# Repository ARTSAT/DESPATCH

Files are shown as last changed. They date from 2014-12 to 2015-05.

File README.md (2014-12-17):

Hardware / Software design of ARTSAT2:DESPATCH
========
This repository is for hardware / software design of ARTSAT2:DESPATCH.  

o spacecraft/body : contains DESPATCH's body design and CAD data.  
o spacecraft/main : contains main OBC's CAD data and source codes.  
o spacecraft/mission : contains mission OBC's CAD data and source codes.  
o ground_station/decoder :  contains telemetry decoding software.  
o ground_station/tracker :  contains tracking software.  
o ground_station/server : contains API server software.  
o ground_station/utility : contains some utility software such as a viewer or an editor, etc...  
o document : contains some specifications of morse and baudot code format, etc...

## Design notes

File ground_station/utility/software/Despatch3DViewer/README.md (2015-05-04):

Despatch3DViewer
====
A 3D viewer for DESPATCH, writted in Javascript.

## Description

[DESPATCH](http://artsat.jp/en/project/despatch), a micro space-probe developed by ARTSAT project, can be viewed on your browser. 
You can zoom in/out and rotate the spacecraft.

## Demo

http://mokk.net/despatch3d/

## Screen shot

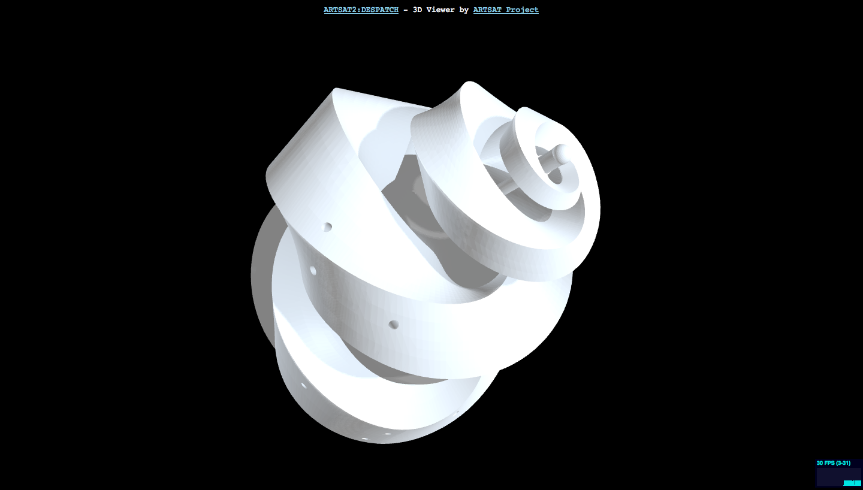
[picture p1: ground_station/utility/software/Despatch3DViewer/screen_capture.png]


## Requirement

A browser that supports WebGL (Google Chrome is recommended).

## Licence

This software is released under the MIT License, see LICENSE.txt.

## Author

[Motoki Kimura](https://github.com/motokimura)

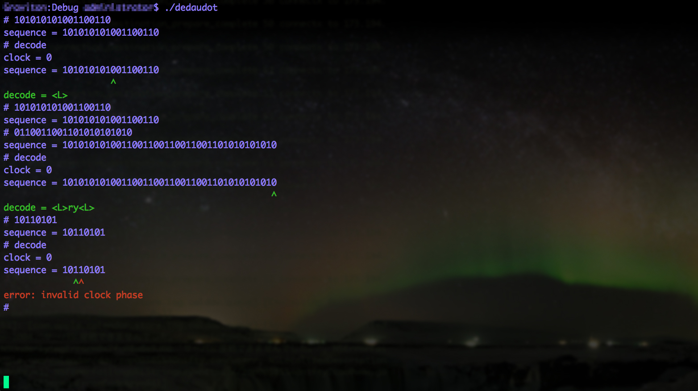
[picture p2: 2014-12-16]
ground_station/decoder/software/debaudot/debaudot_screen2.jpg

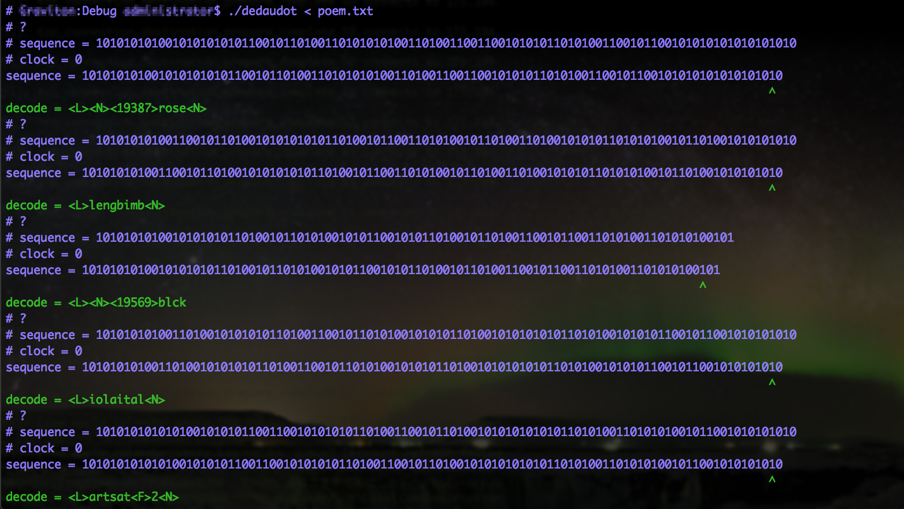
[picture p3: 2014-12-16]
ground_station/decoder/software/debaudot/debaudot_screen1.jpg

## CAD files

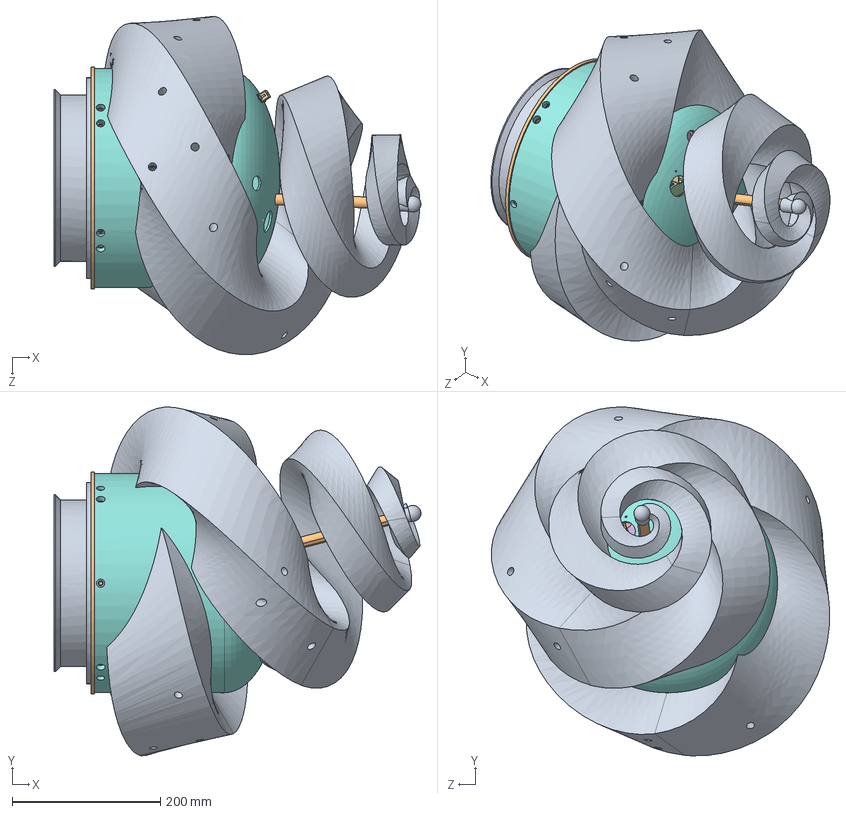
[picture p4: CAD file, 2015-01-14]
spacecraft/body/hardware/SOLIDWORKS/FM_ver1_4/DESPATCH_Assembly.SLDASM
495.6 x 470.8 x 456.7 mm
PAF_interface_frame
Base_Plate2
battery_case_bottom
Aluminium_Keel
Battery x 14
Battery_Case_Top
M3×25_spacer x 4
Aluminium_Cover
Sculpture
Support_rod
Dsub_9pin_female
OBC
M3×5_spacer x 4
Transmitter
Electromagnetic_Shield
Supporting_pole x 6
M2.6×2_spacer x 2
Battery_hub_board
M3×12CAP x 4
hub_insulator
M2.6×15CAP x 2
M2.5_nut x 2
Dsub_9pin_male

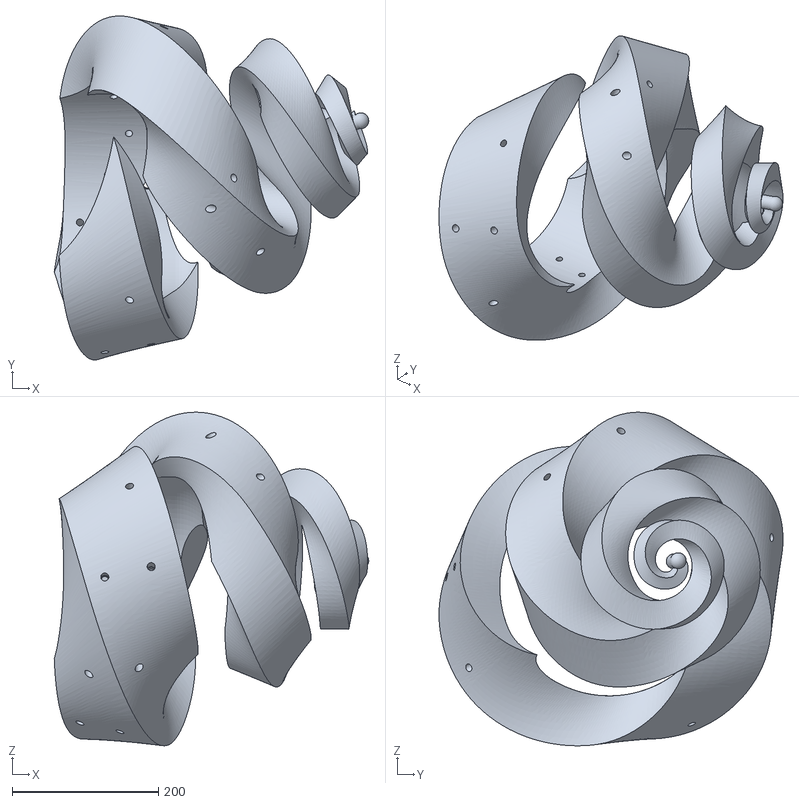
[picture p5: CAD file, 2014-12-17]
ground_station/utility/software/Despatch3DViewer/models/despatch_uzumaki.stl
430.8 x 471.2 x 457.0

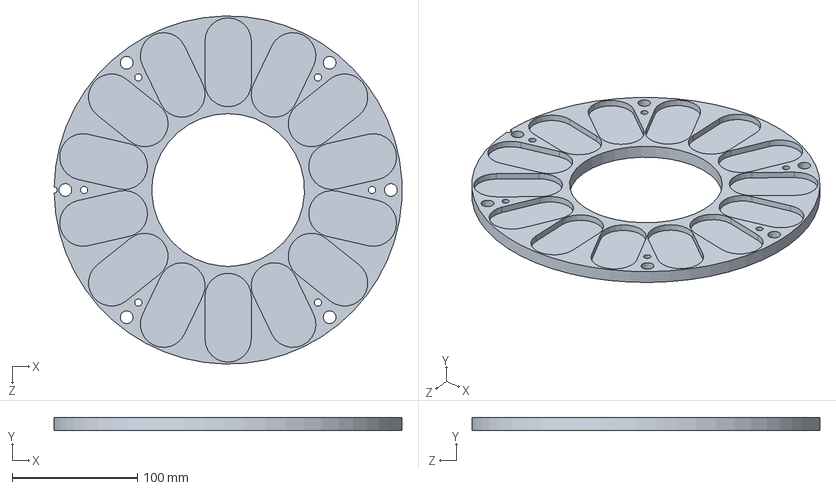
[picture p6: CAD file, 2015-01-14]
spacecraft/body/hardware/SOLIDWORKS/FM_ver1_4/Battery_Case_Bottom.SLDPRT
277.7 x 10.0 x 277.9 mm

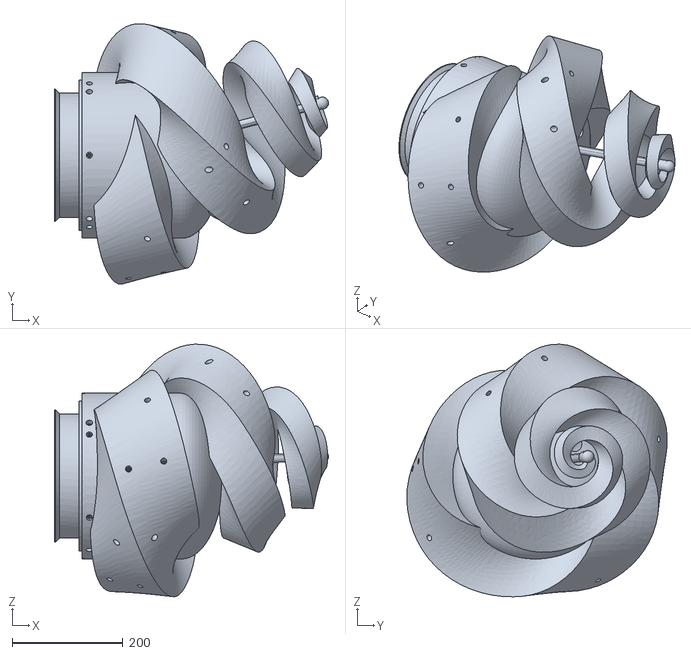
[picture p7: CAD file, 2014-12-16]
spacecraft/body/hardware/STL/FM_ver1.3.STL
495.5 x 470.9 x 456.9

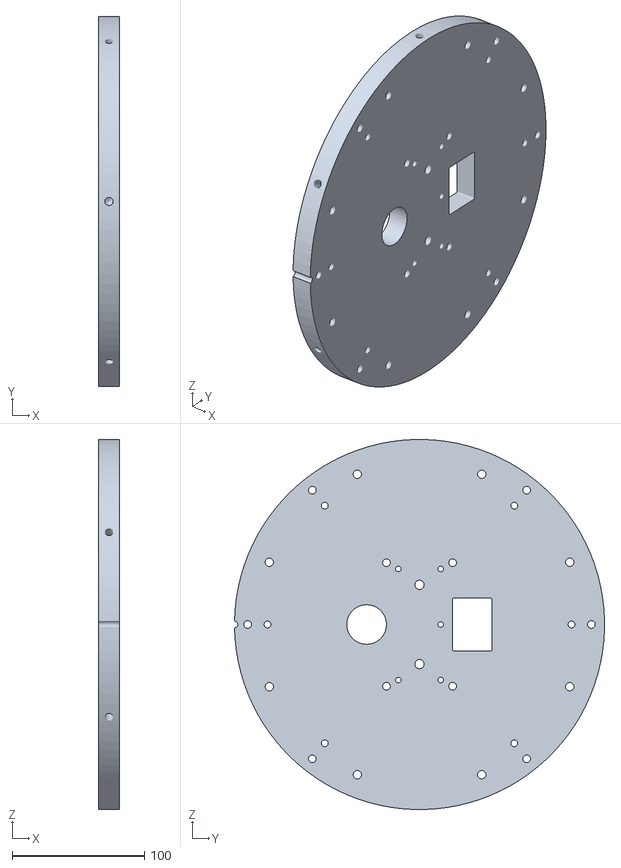
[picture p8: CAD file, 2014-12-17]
ground_station/utility/software/Despatch3DViewer/models/despatch_base.stl
16.0 x 279.9 x 280.0

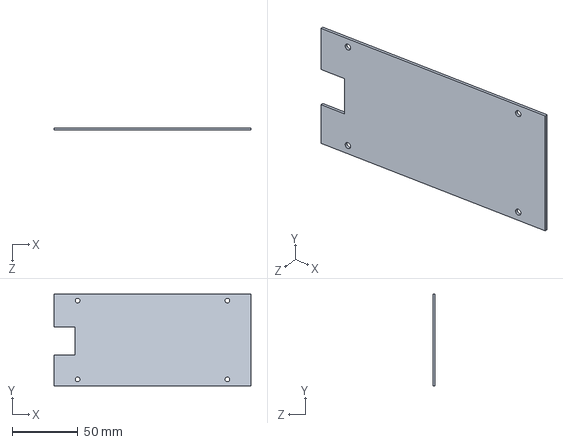
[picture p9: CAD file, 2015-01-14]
spacecraft/body/hardware/SOLIDWORKS/FM_ver1_4/OBC.SLDPRT
150.0 x 70.0 x 1.60 mm

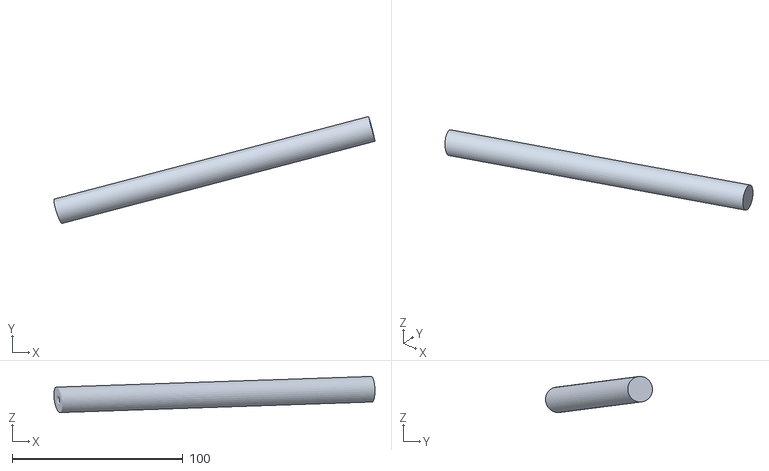
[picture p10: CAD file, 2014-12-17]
ground_station/utility/software/Despatch3DViewer/models/despatch_stay.stl
188.1 x 62.7 x 21.2

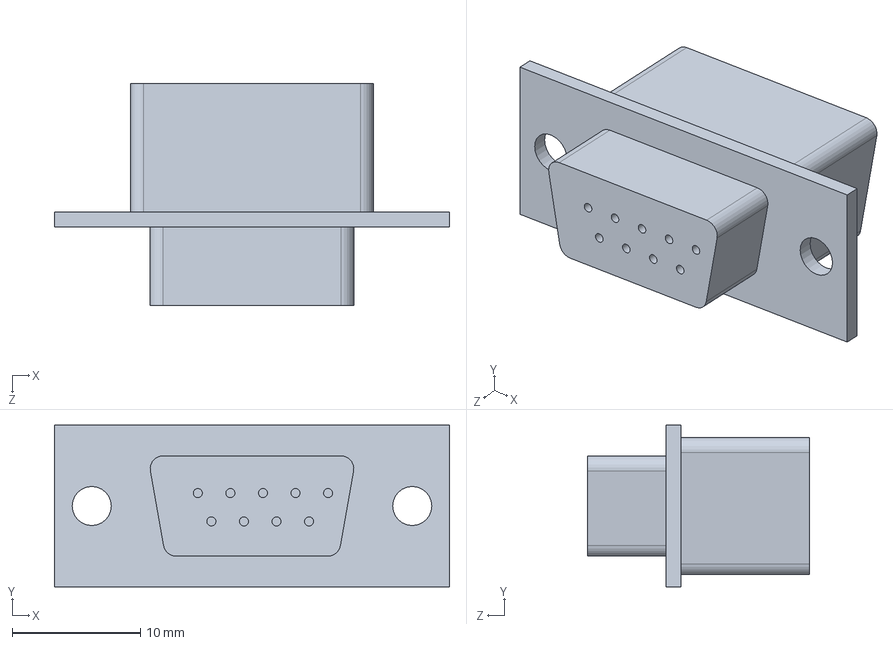
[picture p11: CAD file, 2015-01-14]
spacecraft/body/hardware/SOLIDWORKS/FM_ver1_4/Dsub_9pin_female.SLDPRT
30.8 x 12.6 x 17.3 mm

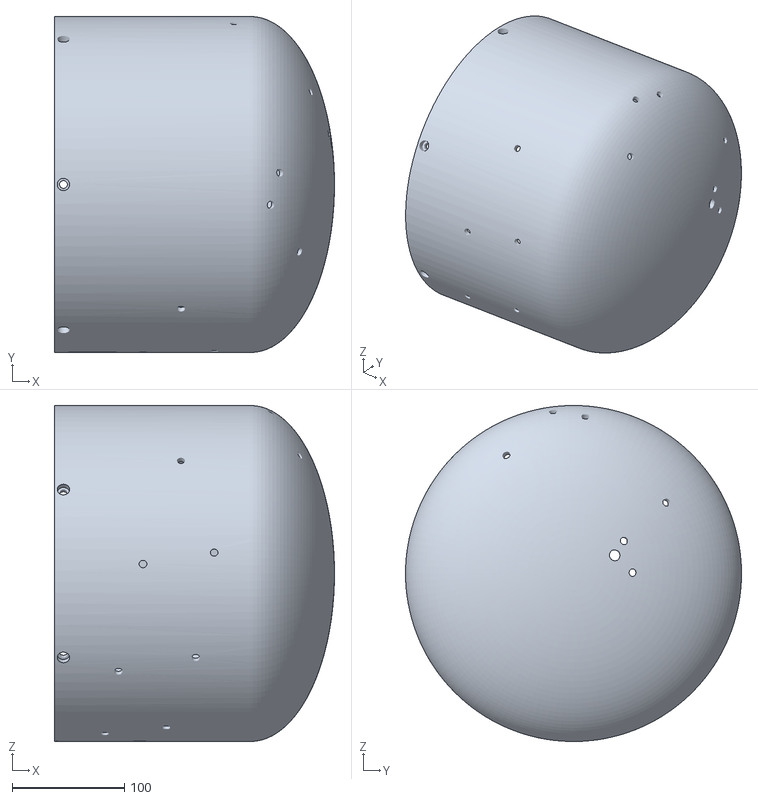
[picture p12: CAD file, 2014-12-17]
ground_station/utility/software/Despatch3DViewer/models/despatch_cover.stl
250.0 x 300.0 x 300.0

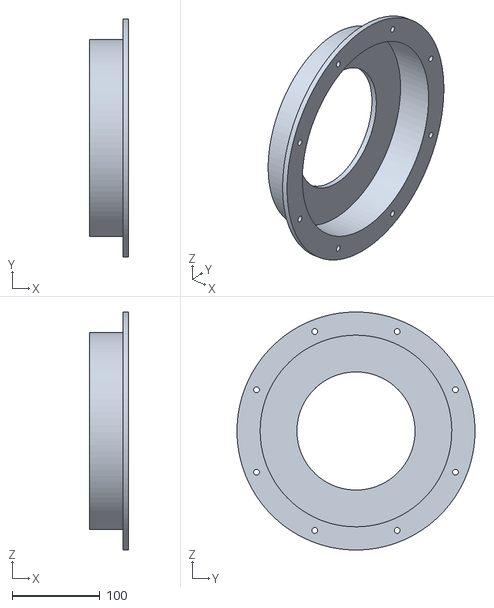
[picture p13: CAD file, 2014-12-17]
ground_station/utility/software/Despatch3DViewer/models/despatch_pafif.stl
44.0 x 272.0 x 272.0

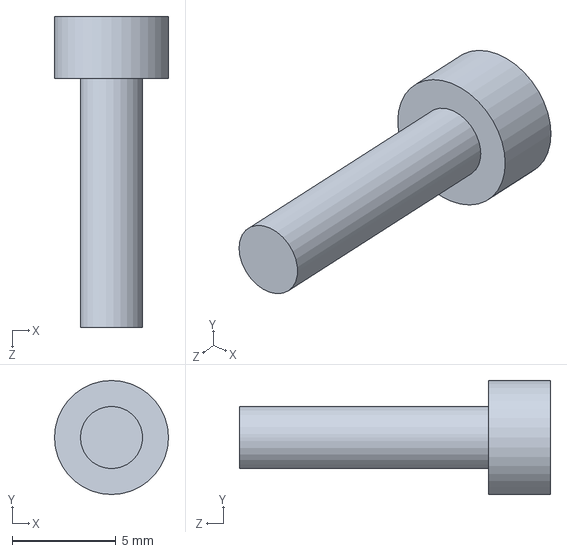
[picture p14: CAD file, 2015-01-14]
spacecraft/body/hardware/SOLIDWORKS/FM_ver1_4/M3×12CAP.SLDPRT
5.50 x 5.50 x 15.0 mm

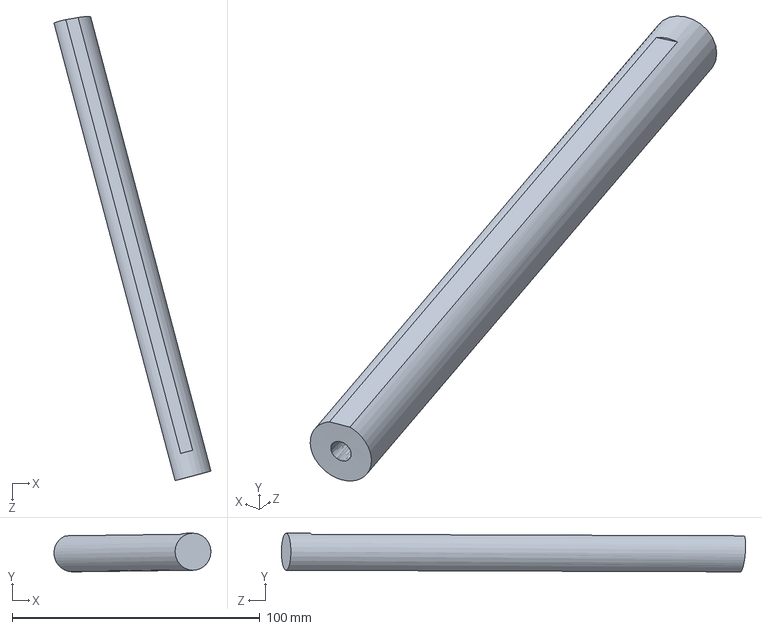
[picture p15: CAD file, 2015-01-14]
spacecraft/body/hardware/SOLIDWORKS/FM_ver1_4/Support_rod.SLDPRT
63.3 x 15.6 x 187.3 mm

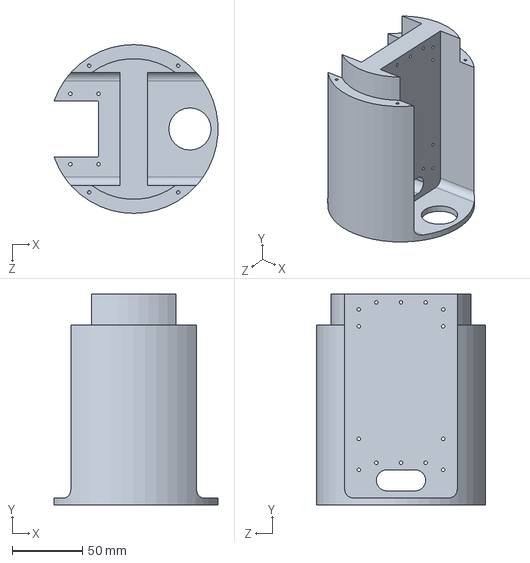
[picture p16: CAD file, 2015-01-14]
spacecraft/body/hardware/SOLIDWORKS/FM_ver1_4/Aluminium_Keel.SLDPRT
116.4 x 150.0 x 120.0 mm

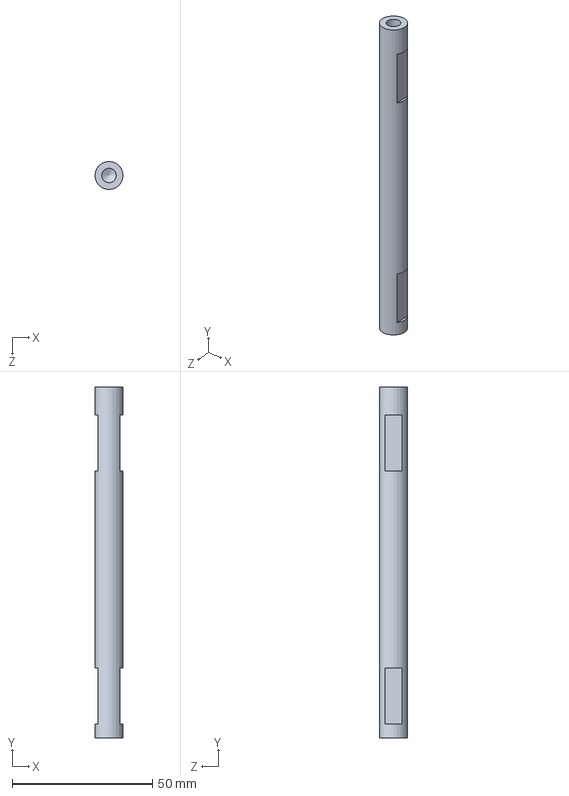
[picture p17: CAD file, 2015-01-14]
spacecraft/body/hardware/SOLIDWORKS/FM_ver1_4/Supporting_pole.SLDPRT
10.0 x 125.0 x 10.0 mm

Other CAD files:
spacecraft/body/hardware/SOLIDWORKS/FM_ver1_4/Transmitter.SLDPRT
spacecraft/body/hardware/SOLIDWORKS/FM_ver1_4/Base_Plate2.SLDPRT
spacecraft/body/hardware/SOLIDWORKS/FM_ver1_4/Battery.SLDPRT
spacecraft/body/hardware/SOLIDWORKS/FM_ver1_4/M3×5_spacer.SLDPRT
spacecraft/body/hardware/SOLIDWORKS/FM_ver1_4/Aluminium_Cover.SLDPRT
spacecraft/body/hardware/SOLIDWORKS/FM_ver1_4/Battery_Case_Top.SLDPRT
spacecraft/body/hardware/SOLIDWORKS/FM_ver1_4/Battery_hub_board.SLDPRT
spacecraft/body/hardware/SOLIDWORKS/FM_ver1_4/Dsub_9pin_male.SLDPRT
spacecraft/body/hardware/SOLIDWORKS/FM_ver1_4/Electromagnetic_Shield.SLDPRT
spacecraft/body/hardware/SOLIDWORKS/FM_ver1_4/M2.5_nut.SLDPRT
spacecraft/body/hardware/SOLIDWORKS/FM_ver1_4/M2.6×15CAP.SLDPRT
spacecraft/body/hardware/SOLIDWORKS/FM_ver1_4/M2.6×2_spacer.SLDPRT
spacecraft/body/hardware/SOLIDWORKS/FM_ver1_4/M3×25_spacer.SLDPRT
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

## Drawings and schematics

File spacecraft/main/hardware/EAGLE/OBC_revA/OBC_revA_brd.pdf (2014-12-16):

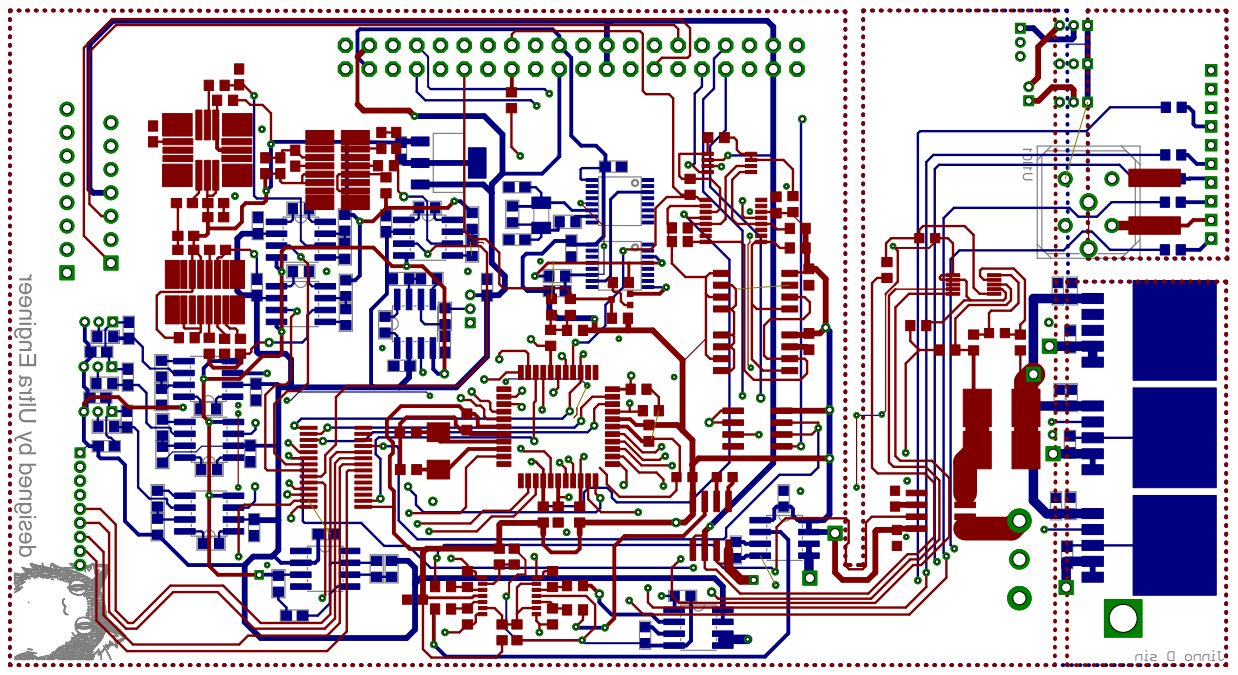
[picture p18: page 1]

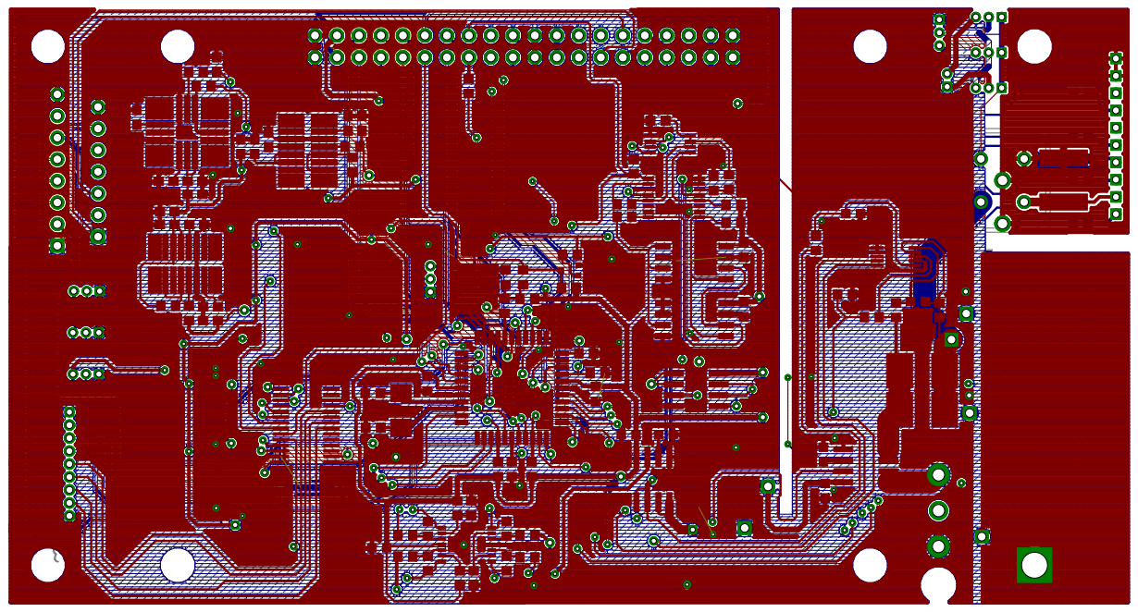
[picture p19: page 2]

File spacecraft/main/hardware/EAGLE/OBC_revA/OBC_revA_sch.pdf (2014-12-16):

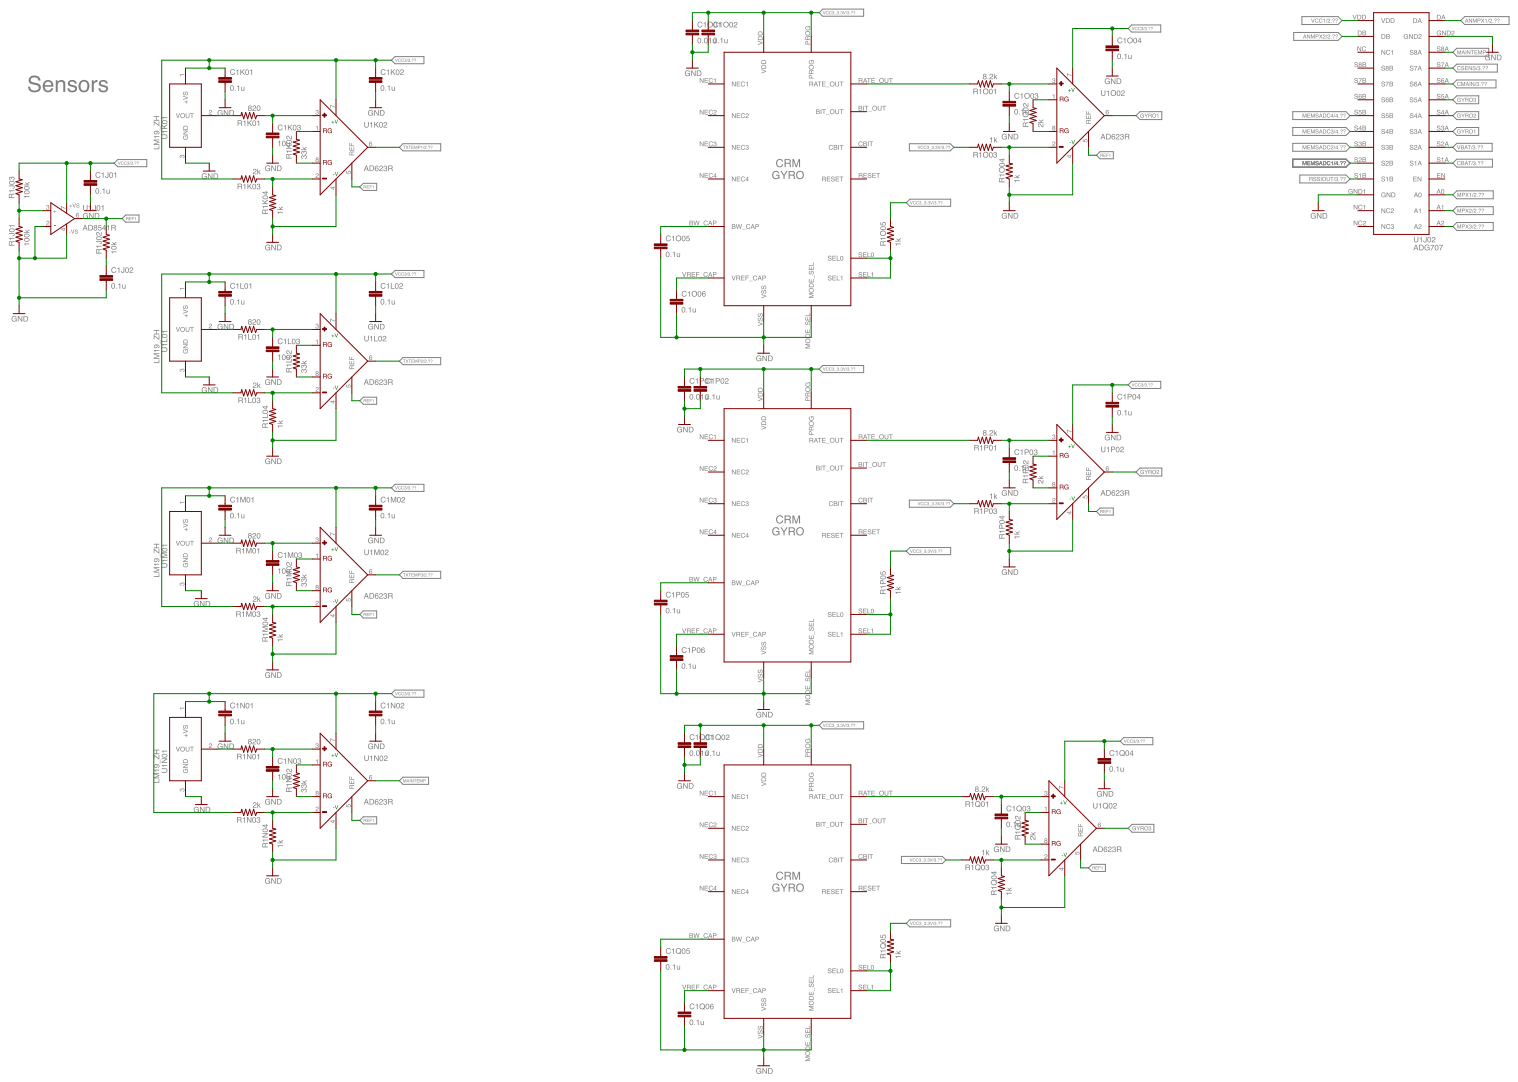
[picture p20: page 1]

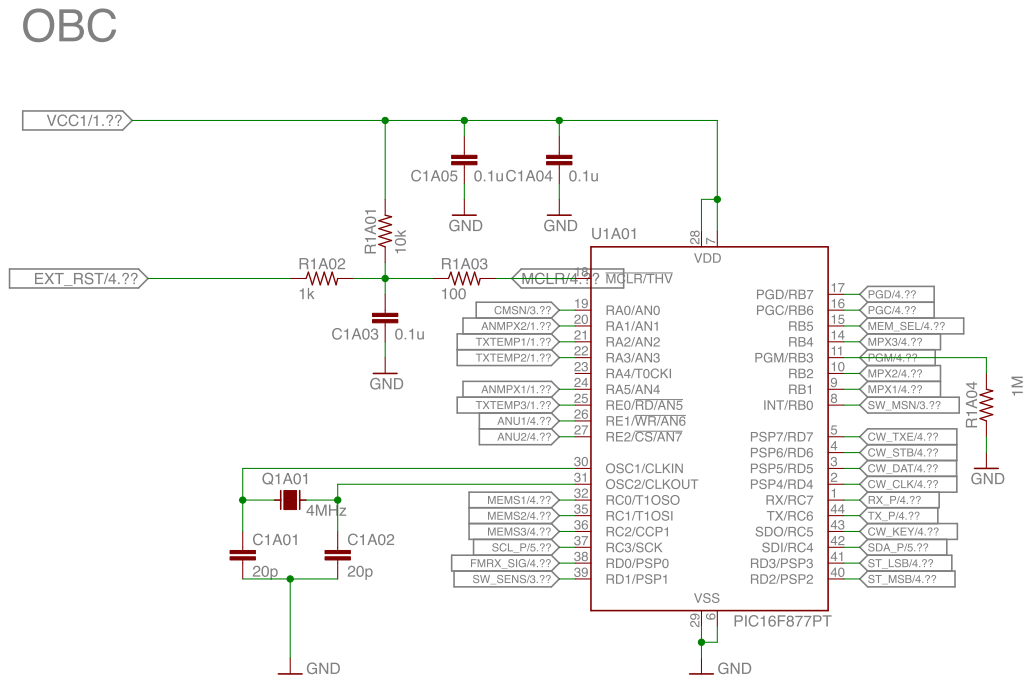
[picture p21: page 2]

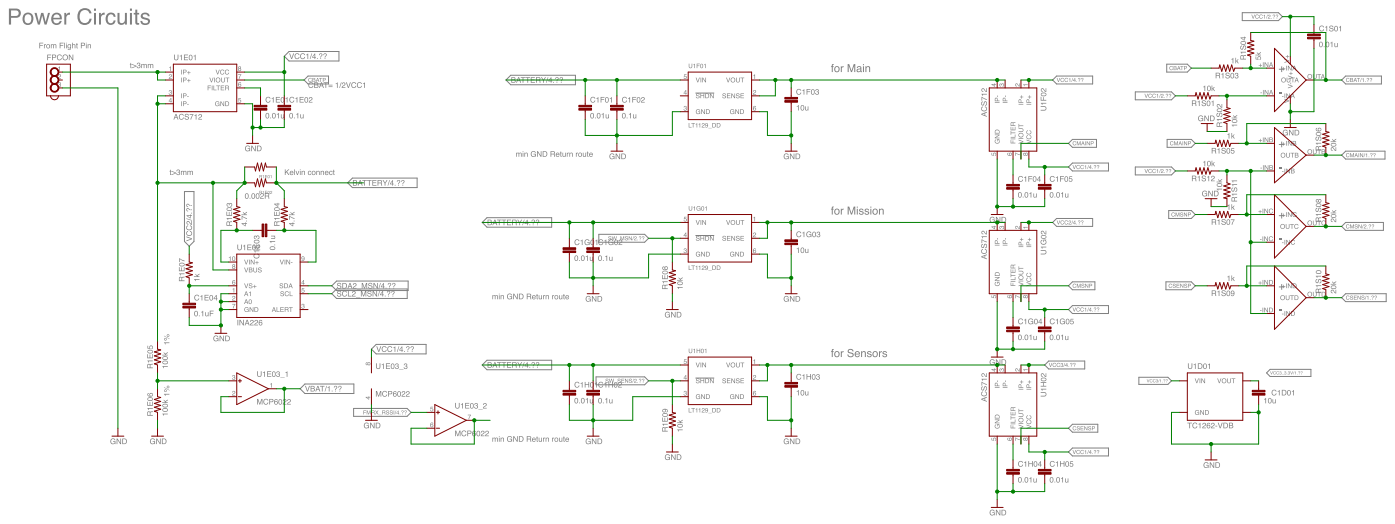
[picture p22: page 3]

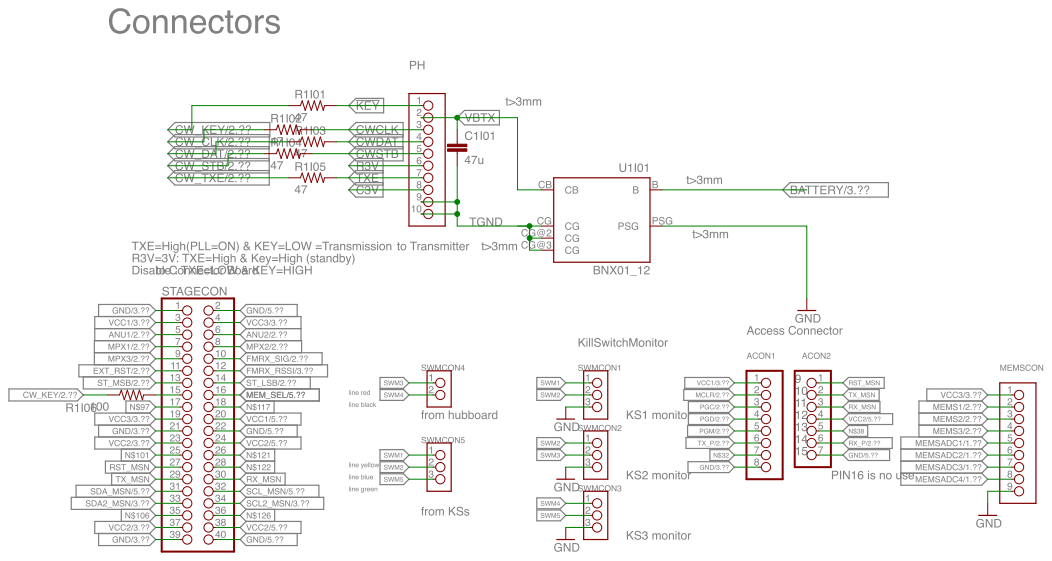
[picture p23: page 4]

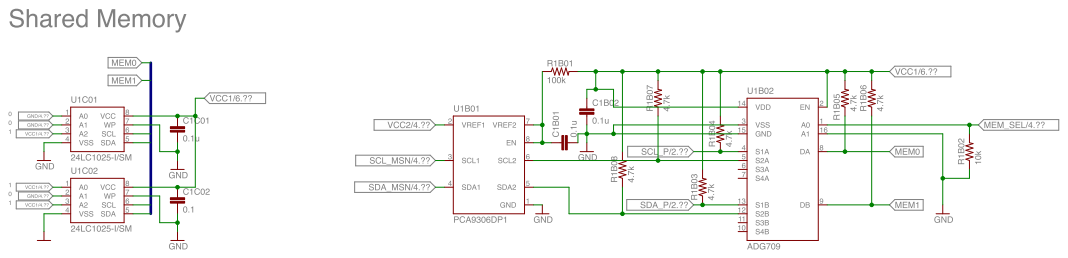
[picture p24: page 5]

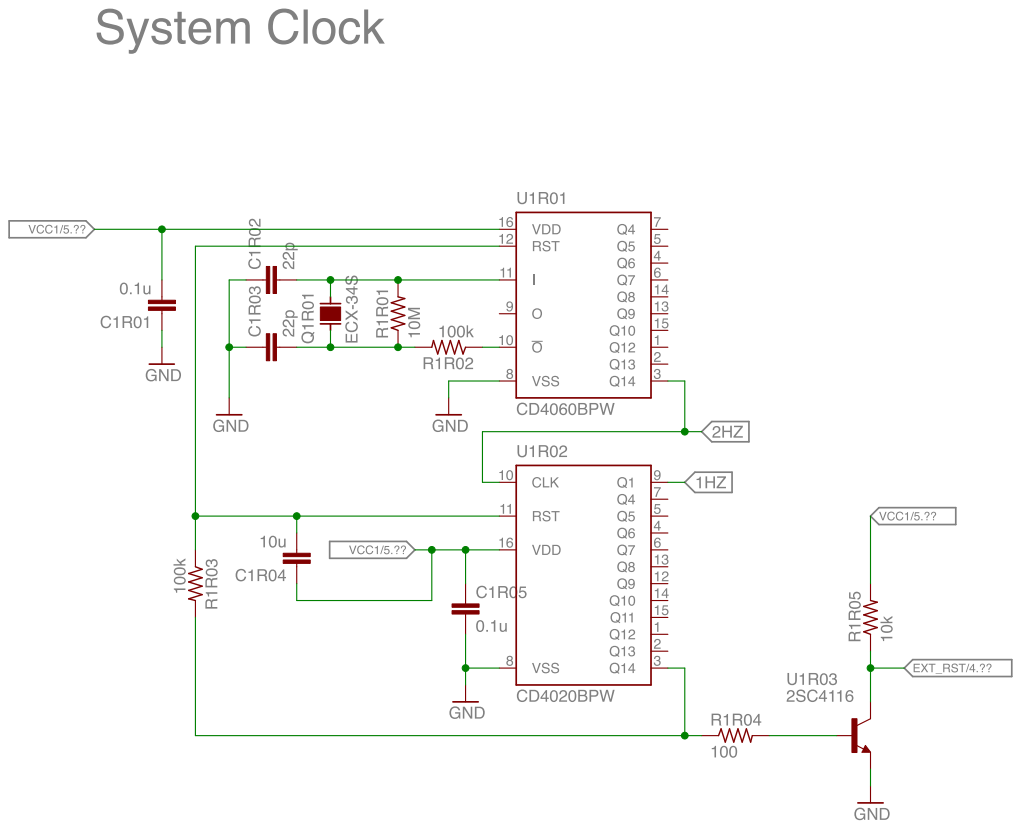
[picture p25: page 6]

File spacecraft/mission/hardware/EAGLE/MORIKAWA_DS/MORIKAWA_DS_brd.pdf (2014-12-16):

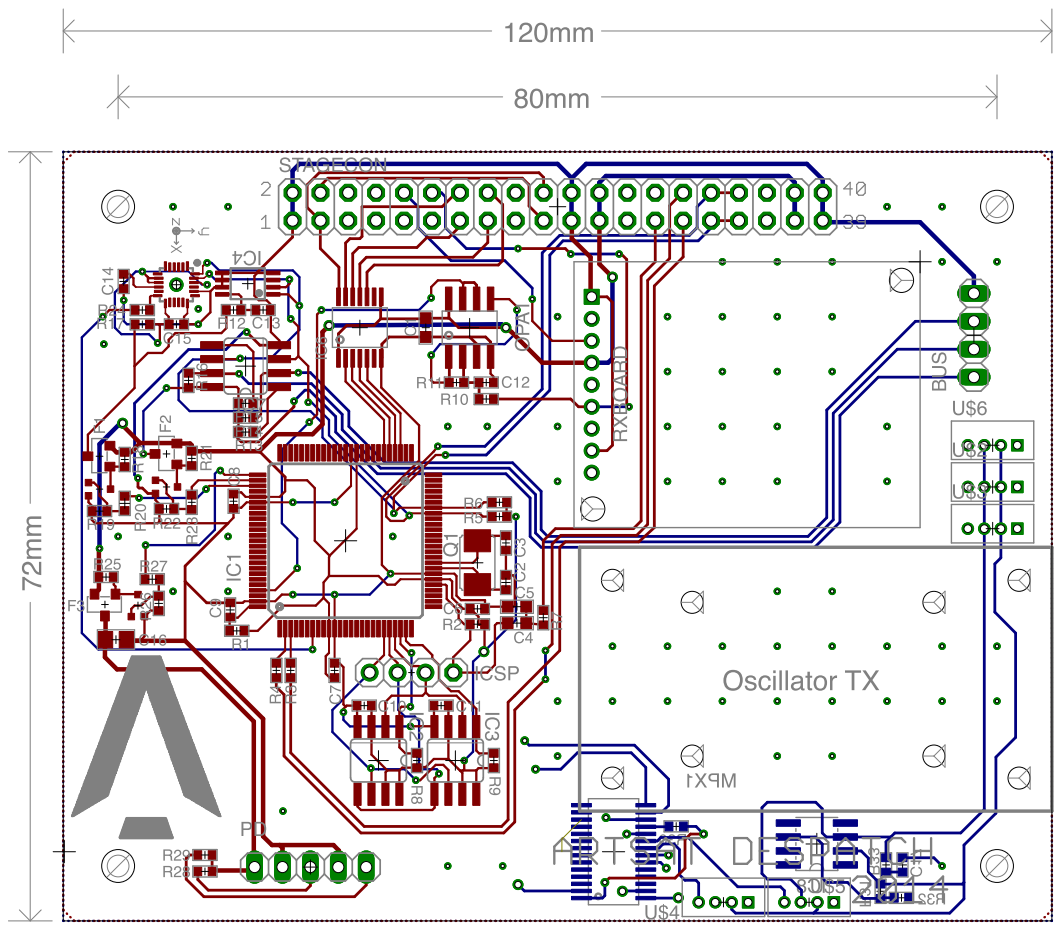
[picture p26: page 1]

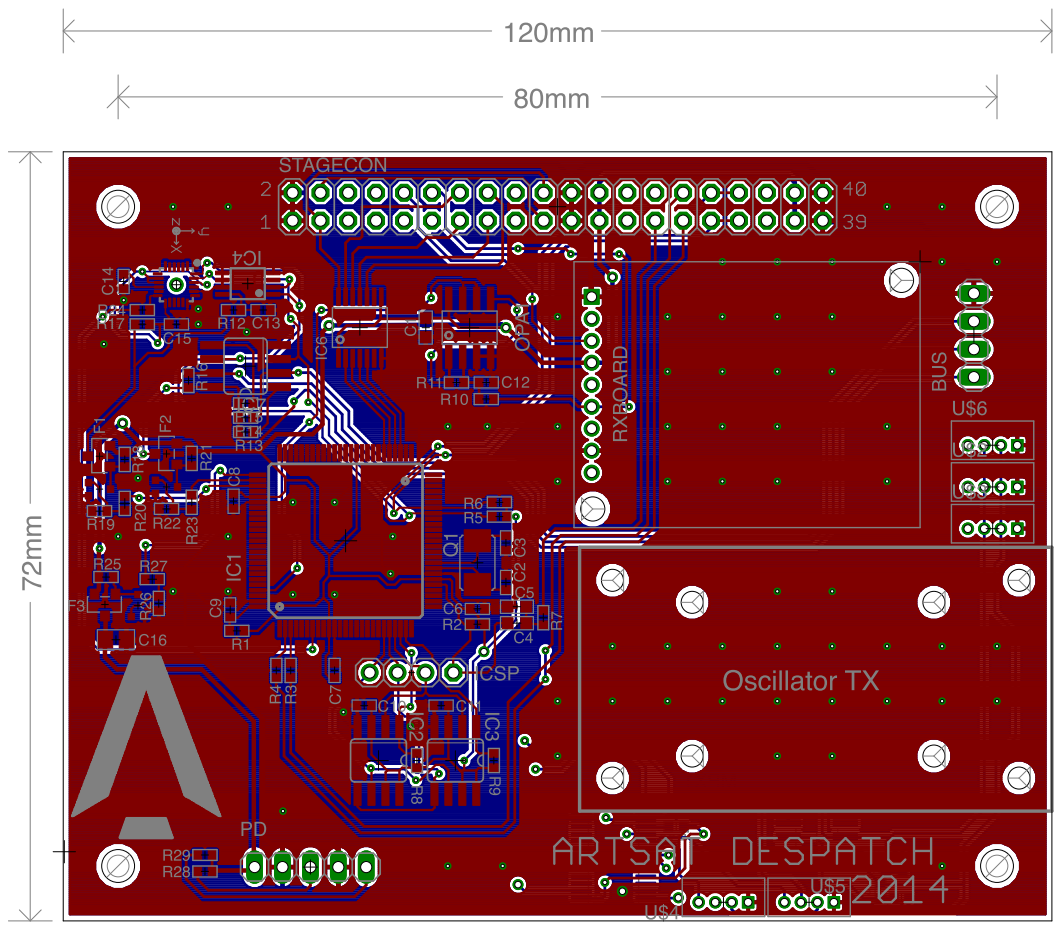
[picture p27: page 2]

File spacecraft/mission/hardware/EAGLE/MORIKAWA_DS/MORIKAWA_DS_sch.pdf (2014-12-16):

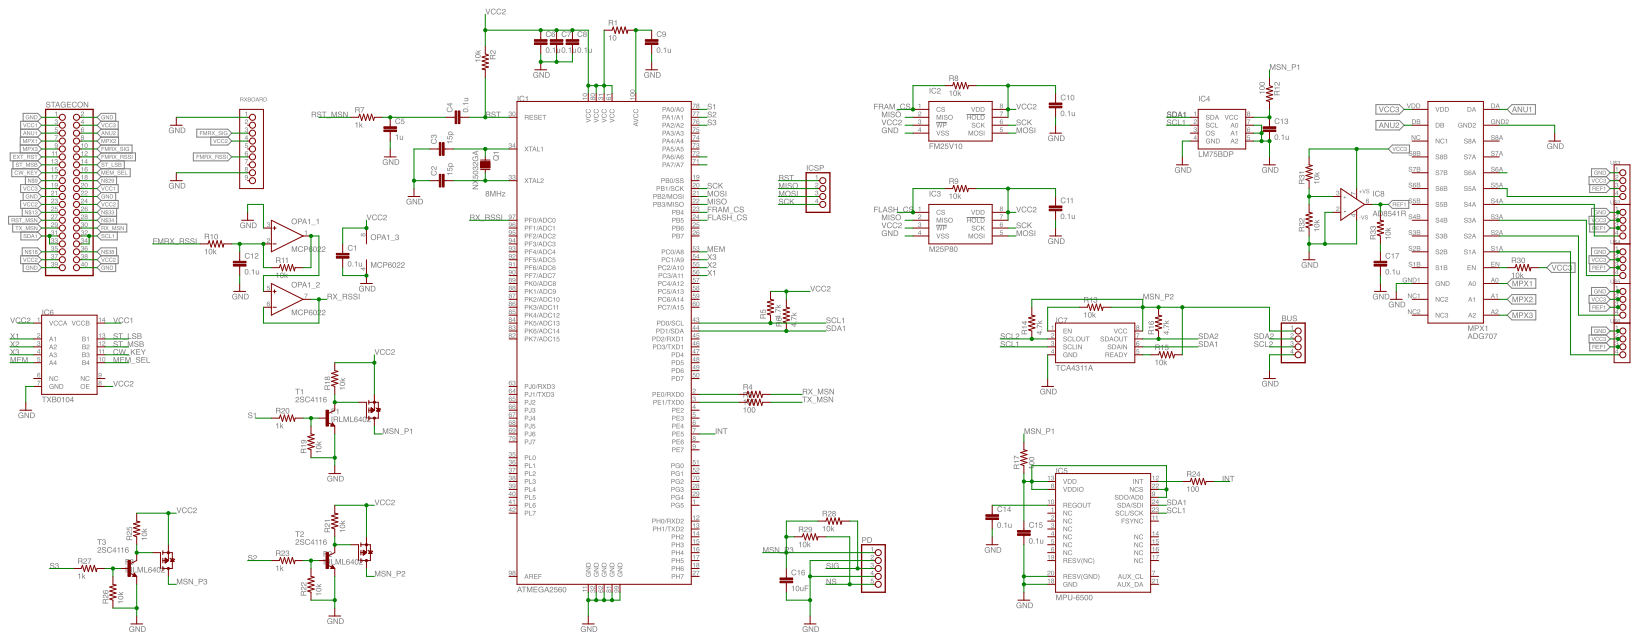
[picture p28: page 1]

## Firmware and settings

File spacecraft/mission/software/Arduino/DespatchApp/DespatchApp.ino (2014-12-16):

/*
**      ARTSAT Despatch Application
**
**      Original Copyright (C) 2014 - 2014 HORIGUCHI Junshi.
**                                          http://iridium.jp/
**                                          zap00365@nifty.com
**      Portions Copyright (C) <year> <author>
**                                          <website>
**                                          <e-mail>
**      All rights reserved.
**
**      Version     Arduino
**      Website     http://artsat.jp/
**      E-mail      info@artsat.jp
**
**      This source code is for Arduino IDE.
**      Arduino 1.0.5
**
**      DespatchApp.ino
**
**      ------------------------------------------------------------------------
**
**      GNU GENERAL PUBLIC LICENSE (GPLv3)
**
**      This program is free software: you can redistribute it and/or modify
**      it under the terms of the GNU General Public License as published by
**      the Free Software Foundation, either version 3 of the License,
**      or (at your option) any later version.
**      This program is distributed in the hope that it will be useful,
**      but WITHOUT ANY WARRANTY; without even the implied warranty of
**      MERCHANTABILITY or FITNESS FOR A PARTICULAR PURPOSE.
**      See the GNU General Public License for more details.
**      You should have received a copy of the GNU General Public License
**      along with this program. If not, see <http://www.gnu.org/licenses/>.
**
**      このプログラムはフリーソフトウェアです。あなたはこれをフリーソフトウェア財団によって発行された
**      GNU 一般公衆利用許諾書（バージョン 3 か、それ以降のバージョンのうちどれか）が定める条件の下で
**      再頒布または改変することができます。このプログラムは有用であることを願って頒布されますが、
**      *全くの無保証* です。商業可能性の保証や特定目的への適合性は、言外に示されたものも含め全く存在しません。
**      詳しくは GNU 一般公衆利用許諾書をご覧ください。
**      あなたはこのプログラムと共に GNU 一般公衆利用許諾書のコピーを一部受け取っているはずです。
**      もし受け取っていなければ <http://www.gnu.org/licenses/> をご覧ください。
*/

#include <MorikawaSDK.h>
#include "utility/I2Cm.h"
#include "WordTable.h"

#define TARGET_BUILD_DEBUG
//#define TARGET_DEBUG_AUTO

//#define TARGET_USE_RADIO

#define PIN_MODE_SELECT_MSB         (34)
#define PIN_MODE_SELECT_LSB         (35)
#define PIN_MPU6500_INT             (3)
#define PIN_RADIO_SIGNAL            (5)
#define PIN_RADIO_NOISE             (2)
#define PIN_RSSI                    (A0)
#define I2C_LM75A_BOARD             (0x48)
#define I2C_LM75A_TX                (0x49)
#define I2C_LM75A_BATTERY           (0x4A)
#define I2C_LM75A_WALL              (0x4B)
#define I2C_LM75A_KEEL              (0x4C)
#define I2C_MPU6500                 (0x69)
#define I2C_INA226                  (0x40)
#define SMEM_GYRO_X                 (0x3FA00UL)
#define SMEM_GYRO_Y                 (0x3FA01UL)
#define SMEM_GYRO_Z                 (0x3FA02UL)
#define SMEM_BATTERY_CURRENT        (0x3FA03UL)
#define SMEM_BATTERY_VOLTAGE        (0x3FA04UL)
#define SMEM_RSSI                   (0x3FA05UL)
#define SMEM_BOARD_TEMPERATURE      (0x3FA06UL)
#define EMEM_CONTEXT_INDEX          (0)
#define INDEX_LIMIT                 (0x300)
#define COUNT_LIMIT                 (8)
#define AVERAGE_SIZE                (3)
#define RANGE_TEMPERATURE_MAXIMUM   (+250)
#define RANGE_TEMPERATURE_MINIMUM   (-110)
#define RANGE_ACCEL_MAXIMUM         (+32767)
#define RANGE_ACCEL_MINIMUM         (-32768)
#define RANGE_GYRO_MAXIMUM          (+32767)
#define RANGE_GYRO_MINIMUM          (-32768)
#define RANGE_VOLTAGE_MAXIMUM       (+32767)
#define RANGE_VOLTAGE_MINIMUM       (0)
#define RANGE_CURRENT_MAXIMUM       (+32767)
#define RANGE_CURRENT_MINIMUM       (-32768)
#define RANGE_RSSI_MAXIMUM          (+1023)
#define RANGE_RSSI_MINIMUM          (0)
#define RANGE_RADIO_MAXIMUM         (+32767)
#define RANGE_RADIO_MINIMUM         (0)
#define LIMIT_TEMPERATURE_MAXIMUM   (19296) // +102 (+51degC)
#define LIMIT_TEMPERATURE_MINIMUM   (7827)  // -24 (-12degC)
#define LIMIT_GYRO_MAXIMUM          (17039) // +1311 (+10deg/sec)
#define LIMIT_GYRO_MINIMUM          (15728) // -1311 (-10deg/sec)
#define LIMIT_CURRENT_MAXIMUM       (18633) // +4500 (+4.5A)
#define LIMIT_CURRENT_MINIMUM       (16133) // -500 (-0.5A)
#define WAIT_LM75A                  (350)   // typical 100ms, limits 300ms
#define WAIT_MPU6500                (300)   // accel = 4 ~ 4000Hz, gyro = 4 ~ 8000Hz
#define WAIT_INA226                 (15)    // typical 140us, limits 154us ~ typical 8.244ms, limits 9.068ms
#define WAIT_ANALOGREAD             (15)    // typical 100us
#define DELAY_RADIO                 (5000)
#define INTERVAL_RADIO              (15000)
#define INVALID_VALUE_4             ("____")
#define INVALID_VALUE_8             ("________")
#define REMAP(v, if, it, of, ot)    (map(constrain((v), (if), (it)), (if), (it), (of), (ot)))

enum ValidEnum {
    VALID_LM75A_BOARD               = 1 << 0,
    VALID_LM75A_TX                  = 1 << 1,
    VALID_LM75A_BATTERY             = 1 << 2,
    VALID_LM75A_WALL                = 1 << 3,
    VALID_LM75A_KEEL                = 1 << 4,
    VALID_MPU6500                   = 1 << 5,
    VALID_INA226                    = 1 << 6
};

static void samplingSensorCold(void);
static void samplingSensorHot(void);
static void samplingRadio(void);
static void clear(int param[AVERAGE_SIZE]);
static int average(int param[AVERAGE_SIZE]);
static void saveIndex(unsigned int param);
static unsigned int loadIndex(void);
static TSTError checkLM75A(int i2c);
static TSTError checkMPU6500(int i2c);
static TSTError checkINA226(int i2c);
static TSTError calibrateLM75A(int i2c);
static TSTError calibrateMPU6500(int i2c);
static TSTError calibrateINA226(int i2c);
static TSTError getLM75A(int i2c, int* temperature);
static TSTError getMPU6500(int i2c, int* ax, int* ay, int* az, int* gx, int* gy, int* gz);
static TSTError getINA226(int i2c, int* voltage, int* current);
static void remapRange(int value, int minimum, int maximum, int* result, bool* remap);
static void makeBaudotFixed(char* buffer, char const PROGMEM* value);
static void makeBaudotState(char* buffer, int loop, int temperature, int rssi, int voltage);
static void makeBaudotColor(char* buffer, int lvalue, bool lvalid, int rvalue, bool rvalid);
static void makeBaudotRhythm(char* buffer, int lvalue, bool lvalid, int rvalue, bool rvalid);
static void dump(TSTError error, int hint);

static TSTTrinity<unsigned char> g_valid;   // bit field as ValidEnum
static TSTTrinity<int> g_board_t;           // [0, 32768), -1 is invalid
static TSTTrinity<int> g_tx_t;              // [0, 32768), -1 is invalid
static TSTTrinity<int> g_battery_t;         // [0, 32768), -1 is invalid
static TSTTrinity<int> g_wall_t;            // [0, 32768), -1 is invalid
static TSTTrinity<int> g_keel_t;            // [0, 32768), -1 is invalid
static TSTTrinity<int> g_gyro_x;            // [0, 32768), -1 is invalid
static TSTTrinity<int> g_gyro_y;            // [0, 32768), -1 is invalid
static TSTTrinity<int> g_gyro_z;            // [0, 32768), -1 is invalid
static TSTTrinity<int> g_battery_v;         // [0, 32768), -1 is invalid
static TSTTrinity<int> g_battery_c;         // [0, 32768), -1 is invalid
static TSTTrinity<int> g_rssi;              // [0, 32768), -1 is invalid
static TSTTrinity<int> g_radio_s;           // [0, 32768), -1 is invalid
static TSTTrinity<int> g_radio_n;           // [0, 32768), -1 is invalid
static TSTTrinity<bool> g_sensor;           // [false, true]
static TSTTrinity<bool> g_poem;             // [false, true]
static TSTTrinity<unsigned int> g_index;    // [0, 0x300)
static TSTTrinity<unsigned int> g_count;    // [0, 8)

void setup(void)
{
#ifdef TARGET_BUILD_DEBUG
    Serial.begin(9600);
#endif
    if (__debug__(Morikawa.setup(), 0) == TSTERROR_OK) {
#ifdef TARGET_BUILD_DEBUG
        //SharedMemory_setup();
        //SharedMemory_loop();
#endif
        __debug__(Morikawa.enablePowerBus(POWER_BUS_Y), 1);
        pinMode(PIN_MODE_SELECT_MSB, INPUT);
        pinMode(PIN_MODE_SELECT_LSB, INPUT);
        pinMode(PIN_MPU6500_INT, INPUT);
        pinMode(PIN_RADIO_SIGNAL, INPUT);
        pinMode(PIN_RADIO_NOISE, INPUT);
        pinMode(PIN_RSSI, INPUT);
        g_valid = 0;
        g_board_t = -1;
        g_tx_t = -1;
        g_battery_t = -1;
        g_wall_t = -1;
        g_keel_t = -1;
        g_gyro_x = -1;
        g_gyro_y = -1;
        g_gyro_z = -1;
        g_battery_v = -1;
        g_battery_c = -1;
        g_rssi = -1;
        g_radio_s = -1;
        g_radio_n = -1;
        g_sensor = true;
        g_poem = true;
        g_index = 0;
        g_count = 0;
        if (__debug__(checkLM75A(I2C_LM75A_BOARD), 10) == TSTERROR_OK) {
            if (__debug__(calibrateLM75A(I2C_LM75A_BOARD), 11) == TSTERROR_OK) {
                g_valid |= VALID_LM75A_BOARD;
            }
        }
        if (__debug__(checkLM75A(I2C_LM75A_TX), 12) == TSTERROR_OK) {
            if (__debug__(calibrateLM75A(I2C_LM75A_TX), 13) == TSTERROR_OK) {
                g_valid |= VALID_LM75A_TX;
            }
        }
        if (__debug__(checkLM75A(I2C_LM75A_BATTERY), 14) == TSTERROR_OK) {
            if (__debug__(calibrateLM75A(I2C_LM75A_BATTERY), 15) == TSTERROR_OK) {
                g_valid |= VALID_LM75A_BATTERY;
            }
        }
        if (__debug__(checkLM75A(I2C_LM75A_WALL), 16) == TSTERROR_OK) {
            if (__debug__(calibrateLM75A(I2C_LM75A_WALL), 17) == TSTERROR_OK) {
                g_valid |= VALID_LM75A_WALL;
            }
        }
        if (__debug__(checkLM75A(I2C_LM75A_KEEL), 18) == TSTERROR_OK) {
            if (__debug__(calibrateLM75A(I2C_LM75A_KEEL), 19) == TSTERROR_OK) {
                g_valid |= VALID_LM75A_KEEL;
            }
        }
        if (__debug__(checkMPU6500(I2C_MPU6500), 20) == TSTERROR_OK) {
            if (__debug__(calibrateMPU6500(I2C_MPU6500), 21) == TSTERROR_OK) {
                g_valid |= VALID_MPU6500;
            }
        }
        if (__debug__(checkINA226(I2C_INA226), 22) == TSTERROR_OK) {
            if (__debug__(calibrateINA226(I2C_INA226), 23) == TSTERROR_OK) {
                g_valid |= VALID_INA226;
            }
        }
        g_index = loadIndex();
        saveIndex(g_index);
#ifdef TARGET_BUILD_DEBUG
        Serial.print("valid = 0b");
        Serial.println(g_valid, BIN);
        Serial.print("index = ");
        Serial.println(g_index);
#endif
    }
    else {
        Morikawa.shutdown();
    }
    return;
}

void loop(void)
{
    bool handle;
    char buffer[16];
    int lvalue;
    int rvalue;
    bool lvalid;
    bool rvalid;
    unsigned long address;
#ifdef TARGET_BUILD_DEBUG
    int debug(Serial.read());
    int i;
#endif
    
    Morikawa.loop();
#ifdef TARGET_BUILD_DEBUG
    if (debug == 'r' || debug == 'R') {
        g_index = 0;
        saveIndex(g_index);
        g_count = 0;
        Serial.print("index = ");
        Serial.println(g_index);
    }
#endif
    handle = false;
#ifdef TARGET_BUILD_DEBUG
    if (debug == 's' || debug == 'S') {
        handle = true;
    }
#else
    if (digitalRead(PIN_MODE_SELECT_MSB) == HIGH) {
        handle = true;
    }
#endif
    if (handle) {
        if (!g_sensor) {
            samplingSensorHot();
            buffer[0] = g_gyro_x >> 7;
            buffer[1] = g_gyro_y >> 7;
            buffer[2] = g_gyro_z >> 7;
            buffer[3] = g_battery_c >> 7;
            buffer[4] = g_battery_v >> 7;
            buffer[5] = g_rssi >> 7;
            buffer[6] = g_board_t >> 7;
            __debug__(Morikawa.writeSharedMemory(SMEM_GYRO_X, buffer, SMEM_BOARD_TEMPERATURE - SMEM_GYRO_X + 1), 30);
#ifdef TARGET_BUILD_DEBUG
            Serial.print("sensor = 0x");
            for (i = 0; i < 6; ++i) {
                Serial.print(static_cast<unsigned char>(buffer[i]), HEX);
                Serial.print(", 0x");
            }
            Serial.println(static_cast<unsigned char>(buffer[6]), HEX);
#endif
            g_sensor = true;
        }
    }
    else if (g_sensor) {
        samplingSensorCold();
        g_sensor = false;
    }
    handle = false;
#ifdef TARGET_BUILD_DEBUG
    if (debug == 'p' || debug == 'P') {
        handle = true;
    }
#ifdef TARGET_DEBUG_AUTO
    if (millis() / 15000 % 2) {
        handle = true;
    }
#endif
#else
    if (digitalRead(PIN_MODE_SELECT_LSB) == HIGH) {
        handle = true;
    }
#endif
    if (handle) {
        if (!g_poem) {
            memset(buffer, 0, sizeof(buffer));
            switch (g_count) {
                case 0:
                    makeBaudotFixed(buffer, PSTR("jqF1Lznn"));
                    break;
                case 1:
                    makeBaudotState(buffer, g_index << 5, g_board_t, g_rssi, g_battery_v);
                    break;
                case 2:
                    remapRange(g_tx_t, LIMIT_TEMPERATURE_MINIMUM, LIMIT_TEMPERATURE_MAXIMUM, &lvalue, &lvalid);
                    remapRange(g_keel_t, LIMIT_TEMPERATURE_MINIMUM, LIMIT_TEMPERATURE_MAXIMUM, &rvalue, &rvalid);
                    makeBaudotColor(buffer, lvalue, lvalid, rvalue, rvalid);
                    break;
                case 3:
                    remapRange(g_battery_t, LIMIT_TEMPERATURE_MINIMUM, LIMIT_TEMPERATURE_MAXIMUM, &lvalue, &lvalid);
                    remapRange(g_wall_t, LIMIT_TEMPERATURE_MINIMUM, LIMIT_TEMPERATURE_MAXIMUM, &rvalue, &rvalid);
                    makeBaudotColor(buffer, lvalue, lvalid, rvalue, rvalid);
                    break;
                case 4:
                    remapRange(g_gyro_x, LIMIT_GYRO_MINIMUM, LIMIT_GYRO_MAXIMUM, &lvalue, &lvalid);
                    remapRange(g_gyro_y, LIMIT_GYRO_MINIMUM, LIMIT_GYRO_MAXIMUM, &rvalue, &rvalid);
                    makeBaudotRhythm(buffer, lvalue, lvalid, rvalue, rvalid);
                    break;
                case 5:
                    remapRange(g_gyro_z, LIMIT_GYRO_MINIMUM, LIMIT_GYRO_MAXIMUM, &lvalue, &lvalid);
                    remapRange(g_battery_c, LIMIT_CURRENT_MINIMUM, LIMIT_CURRENT_MAXIMUM, &rvalue, &rvalid);
                    makeBaudotRhythm(buffer, lvalue, lvalid, rvalue, rvalid);
                    break;
                case 6:
                    makeBaudotFixed(buffer, PSTR("artsatF2"));
                    break;
                case 7:
                    makeBaudotFixed(buffer, PSTR("despatch"));
                    break;
                default:
                    // nop
                    break;
            }
            address = (static_cast<unsigned long>(g_index) << 8) | (static_cast<unsigned long>(g_count) << 4);
            __debug__(Morikawa.writeSharedMemory(address, buffer, sizeof(buffer)), 31);
#ifdef TARGET_BUILD_DEBUG
            Serial.print("poem [0x");
            Serial.print(address, HEX);
            Serial.print("] = ");
            for (i = 0; i < lengthof(buffer); ++i) {
                if (0 <= buffer[i] && buffer[i] < 32) {
                    Serial.print("<0x");
                    Serial.print(static_cast<unsigned char>(buffer[i]), HEX);
                    Serial.print(">");
                }
                else {
                    Serial.print(buffer[i]);
                }
            }
            Serial.println("");
#endif
            switch (g_count) {
                case 0:
                    samplingSensorHot();
#ifdef TARGET_USE_RADIO
                    samplingRadio();
#endif
                    break;
                default:
                    // nop
                    break;
            }
            if (++g_count >= COUNT_LIMIT) {
                if (++g_index >= INDEX_LIMIT) {
                    g_index = 0;
                }
                saveIndex(g_index);
                g_count = 0;
            }
            g_poem = true;
        }
    }
    else if (g_poem) {
        switch (g_count) {
            case 0:
                samplingSensorCold();
                break;
            default:
                // nop
                break;
        }
        g_poem = false;
    }
    return;
}

void delay10mTimes(unsigned int times)
{
    for (; times > 0; --times) {
        delay(10);
        Morikawa.loop();
    }
    return;
}

TSTError __debug__(TSTError error, int hint)
{
    static TSTTrinity<TSTError> s_error(TSTERROR_OK);
    
    if (error != TSTERROR_OK) {
        if (s_error == TSTERROR_OK) {
            dump(error, hint);
            s_error = error;
        }
    }
    return error;
}

static void samplingSensorCold(void)
{
    int value[AVERAGE_SIZE];
    int i;
    
    for (i = 0; i < AVERAGE_SIZE; ++i) {
        delay(WAIT_ANALOGREAD);
        value[i] = REMAP(analogRead(PIN_RSSI), RANGE_RSSI_MINIMUM, RANGE_RSSI_MAXIMUM, 0, 32767);
#ifdef TARGET_BUILD_DEBUG
        Serial.print("    analogRead RSSI = ");
        Serial.println(value[i]);
#endif
    }
    g_rssi = average(value);
    return;
}

static void samplingSensorHot(void)
{
    int value[6][AVERAGE_SIZE];
    int i;
    
    for (i = 0; i < 5; ++i) {
        clear(value[i]);
    }
    for (i = 0; i < AVERAGE_SIZE; ++i) {
        delay(WAIT_LM75A);
        if (g_valid & VALID_LM75A_BOARD) {
            __debug__(getLM75A(I2C_LM75A_BOARD, &value[0][i]), 50);
        }
        if (g_valid & VALID_LM75A_TX) {
            __debug__(getLM75A(I2C_LM75A_TX, &value[1][i]), 51);
        }
        if (g_valid & VALID_LM75A_BATTERY) {
            __debug__(getLM75A(I2C_LM75A_BATTERY, &value[2][i]), 52);
        }
        if (g_valid & VALID_LM75A_WALL) {
            __debug__(getLM75A(I2C_LM75A_WALL, &value[3][i]), 53);
        }
        if (g_valid & VALID_LM75A_KEEL) {
            __debug__(getLM75A(I2C_LM75A_KEEL, &value[4][i]), 54);
        }
#ifdef TARGET_BUILD_DEBUG
        Serial.print("    LM75A Board = ");
        Serial.print(value[0][i]);
        Serial.print(", TX = ");
        Serial.print(value[1][i]);
        Serial.print(", Battery = ");
        Serial.print(value[2][i]);
        Serial.print(", Wall = ");
        Serial.print(value[3][i]);
        Serial.print(", Keel = ");
        Serial.println(value[4][i]);
#endif
    }
    g_board_t = average(value[0]);
    g_tx_t = average(value[1]);
    g_battery_t = average(value[2]);
    g_wall_t = average(value[3]);
    g_keel_t = average(value[4]);
    for (i = 0; i < 6; ++i) {
        clear(value[i]);
    }
    for (i = 0; i < AVERAGE_SIZE; ++i) {
        delay(WAIT_MPU6500);
        if (g_valid & VALID_MPU6500) {
            __debug__(getMPU6500(I2C_MPU6500, &value[0][i], &value[1][i], &value[2][i], &value[3][i], &value[4][i], &value[5][i]), 60);
        }
#ifdef TARGET_BUILD_DEBUG
        Serial.print("    MPU6500 Accel X = ");
        Serial.print(value[0][i]);
        Serial.print(", Y = ");
        Serial.print(value[1][i]);
        Serial.print(", Z = ");
        Serial.print(value[2][i]);
        Serial.print(", Gyro X = ");
        Serial.print(value[3][i]);
        Serial.print(", Y = ");
        Serial.print(value[4][i]);
        Serial.print(", Z = ");
        Serial.println(value[5][i]);
#endif
    }
    g_gyro_x = average(value[3]);
    g_gyro_y = average(value[4]);
    g_gyro_z = average(value[5]);
    for (i = 0; i < 2; ++i) {
        clear(value[i]);
    }
    for (i = 0; i < AVERAGE_SIZE; ++i) {
        delay(WAIT_INA226);
        if (g_valid & VALID_INA226) {
            __debug__(getINA226(I2C_INA226, &value[0][i], &value[1][i]), 70);
        }
#ifdef TARGET_BUILD_DEBUG
        Serial.print("    INA226 Voltage = ");
        Serial.print(value[0][i]);
        Serial.print(", Current = ");
        Serial.println(value[1][i]);
#endif
    }
    g_battery_v = average(value[0]);
    g_battery_c = average(value[1]);
    return;
}

static void samplingRadio(void)
{
    unsigned long signalCount;
    unsigned long noiseCount;
    bool signalLock;
    bool noiseLock;
    unsigned long base;
    unsigned long time;
    
    __debug__(Morikawa.enablePowerBus(POWER_BUS_Z), 80);
    digitalWrite(PIN_RADIO_SIGNAL, HIGH);
    digitalWrite(PIN_RADIO_NOISE, HIGH);
    delay(DELAY_RADIO);
    signalCount = 0;
    noiseCount = 0;
    signalLock = false;
    noiseLock = false;
    base = millis();
    while (true) {
        time = millis();
        if (time >= base) {
            if (time - base >= INTERVAL_RADIO) {
                break;
            }
        }
        else if (time >= base + INTERVAL_RADIO) {
            break;
        }
        if (!digitalRead(PIN_RADIO_SIGNAL)) {
            if (!signalLock) {
                ++signalCount;
                signalLock = true;
            }
        }
        else {
            signalLock = false;
        }
        if (!digitalRead(PIN_RADIO_NOISE)) {
            if (!noiseLock) {
                ++noiseCount;
                noiseLock = true;
            }
        }
        else {
            noiseLock = false;
        }
    }
#ifdef TARGET_BUILD_DEBUG
    Serial.print("    PGT5 Signal = ");
    Serial.print(signalCount);
    Serial.print(", Noise = ");
    Serial.println(noiseCount);
#endif
    g_radio_s = REMAP(signalCount, RANGE_RADIO_MINIMUM, RANGE_RADIO_MAXIMUM, 0, 32767);
    g_radio_n = REMAP(noiseCount, RANGE_RADIO_MINIMUM, RANGE_RADIO_MAXIMUM, 0, 32767);
    digitalWrite(PIN_RADIO_NOISE, LOW);
    digitalWrite(PIN_RADIO_SIGNAL, LOW);
    Morikawa.disablePowerBus(POWER_BUS_Z);
    return;
}

static void clear(int param[AVERAGE_SIZE])
{
    int i;
    
    for (i = 0; i < AVERAGE_SIZE; ++i) {
        param[i] = -1;
    }
    return;
}

static int average(int param[AVERAGE_SIZE])
{
    long sum;
    int count;
    int i;
    int result(-1);
    
    sum = 0;
    count = 0;
    for (i = 0; i < AVERAGE_SIZE; ++i) {
        if (param[i] >= 0) {
            sum += param[i];
            ++count;
        }
    }
    if (count > 0) {
        result = sum / count;
    }
    return result;
}

static void saveIndex(unsigned int param)
{
    int i;
    
    for (i = 0; i < 3; ++i) {
        __debug__(Morikawa.writeEEPROM(EMEM_CONTEXT_INDEX + i * sizeof(param), &param, sizeof(param)), 100);
    }
    return;
}
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

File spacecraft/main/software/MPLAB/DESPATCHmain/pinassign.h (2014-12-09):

#ifndef _PINASSIGN_H_

#define MEMS0 (PIN_C0)//I/O
#define MEMS1 (PIN_C1)//SPI MISO
#define MEMS2 (PIN_C2)//SPI CLK

//#define SCL PIN_C3
//#define SDA PIN_C4

#define CWKEY (PIN_C5)

//#define TX PIN_C6
//#define RX PIN_C7

#define SWMSN (PIN_B0)
#define MPX1 (PIN_B1)
#define MPX2 (PIN_B2)
//#define PGM PIN_B3
#define MPX3 (PIN_B4)
#define MEMSEL (PIN_B5)
//#define PGC PIN_B6
//#define PGD PIN_B7

#define FMRXSIG (PIN_D0)
#define SWSENS (PIN_D1)
#define STMSB (PIN_D3)
#define STLSB (PIN_D2)

#define CWCLK (PIN_D4)
#define CWDAT (PIN_D5)
#define CWSTB (PIN_D6)
#define CWTXE (PIN_D7)

//#define CMSN PIN_A0
//#define ANMPX2 PIN_A1
//#define TXTEMP1 PIN_A2
//#define TXTEMP2 PIN_A3
//#define RESERVED PIN_A4
//#define ANMPX1 PIN_A5
//#define TXTEMP3 PIN_E0
//#define AUMPX1 PIN_E1
//#define AUMPX2 PIN_E2


#endif

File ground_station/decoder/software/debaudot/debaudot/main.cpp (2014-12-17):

/*
**      ARTSAT Project
**
**      Original Copyright (C) 2014 - 2014 HORIGUCHI Junshi.
**                                          http://iridium.jp/
**                                          zap00365@nifty.com
**      Portions Copyright (C) <year> <author>
**                                          <website>
**                                          <e-mail>
**      Version     POSIX / C++11
**      Website     http://artsat.jp/
**      E-mail      info@artsat.jp
**
**      This source code is for Xcode.
**      Xcode 6.1 (Apple LLVM 6.0)
**
**      main.cpp
**
**      ------------------------------------------------------------------------
**
**      The MIT License (MIT)
**
**      Permission is hereby granted, free of charge, to any person obtaining a copy of this software and
**      associated documentation files (the "Software"), to deal in the Software without restriction,
**      including without limitation the rights to use, copy, modify, merge, publish, distribute,
**      sublicense, and/or sell copies of the Software, and to permit persons to whom the Software is
**      furnished to do so, subject to the following conditions:
**      The above copyright notice and this permission notice shall be included in all copies or
**      substantial portions of the Software.
**      THE SOFTWARE IS PROVIDED "AS IS", WITHOUT WARRANTY OF ANY KIND, EXPRESS OR IMPLIED, INCLUDING
**      BUT NOT LIMITED TO THE WARRANTIES OF MERCHANTABILITY, FITNESS FOR A PARTICULAR PURPOSE AND NONINFRINGEMENT.
**      IN NO EVENT SHALL THE AUTHORS OR COPYRIGHT HOLDERS BE LIABLE FOR ANY CLAIM, DAMAGES OR OTHER LIABILITY,
**      WHETHER IN AN ACTION OF CONTRACT, TORT OR OTHERWISE, ARISING FROM,
**      OUT OF OR IN CONNECTION WITH THE SOFTWARE OR THE USE OR OTHER DEALINGS IN THE SOFTWARE.
**
**      以下に定める条件に従い、本ソフトウェアおよび関連文書のファイル（以下「ソフトウェア」）の複製を
**      取得するすべての人に対し、ソフトウェアを無制限に扱うことを無償で許可します。
**      これには、ソフトウェアの複製を使用、複写、変更、結合、掲載、頒布、サブライセンス、および、または販売する権利、
**      およびソフトウェアを提供する相手に同じことを許可する権利も無制限に含まれます。
**      上記の著作権表示および本許諾表示を、ソフトウェアのすべての複製または重要な部分に記載するものとします。
**      ソフトウェアは「現状のまま」で、明示であるか暗黙であるかを問わず、何らの保証もなく提供されます。
**      ここでいう保証とは、商品性、特定の目的への適合性、および権利非侵害についての保証も含みますが、それに限定されるものではありません。
**      作者または著作権者は、契約行為、不法行為、またはそれ以外であろうと、ソフトウェアに起因または関連し、
**      あるいはソフトウェアの使用またはその他の扱いによって生じる一切の請求、損害、その他の義務について何らの責任も負わないものとします。
*/

#include <iostream>

#define __USE_COLOR

using namespace::std;

static char const* baudot_table_ltrs[] = {
    "N",
    "e",
    "[LF]",
    "a",
    " ",
    "s",
    "i",
    "u",
    "[CR]",
    "d",
    "r",
    "j",
    "n",
    "f",
    "c",
    "k",
    "t",
    "z",
    "l",
    "w",
    "h",
    "y",
    "p",
    "q",
    "o",
    "b",
    "g",
    "F",
    "m",
    "x",
    "v",
    "L"
};
static char const* baudot_table_figs[] = {
    "N",
    "3",
    "[LF]",
    "-",
    " ",
    "'",
    "8",
    "7",
    "[CR]",
    "$",
    "4",
    "'",
    ",",
    "!",
    ":",
    "(",
    "5",
    "+",
    ")",
    "2",
    "*",
    "6",
    "0",
    "1",
    "9",
    "?",
    "&",
    "F",
    ".",
    "/",
    ";",
    "L"
};

bool is_01(string const& param)
{
    int i;
    bool result(true);
    
    for (i = 0; i < param.size(); ++i) {
        if (!(param[i] == '0' || param[i] == '1')) {
            result = false;
        }
    }
    return result;
}

bool demanchester(string const& param, bool clock, string* decode, int* size)
{
    int i;
    bool result(true);
    
    decode->clear();
    *size = 0;
    if (!clock) {
        for (i = 0; i < param.size() / 2; ++i) {
            if (param[i * 2 + 0] == '1' && param[i * 2 + 1] == '0') {
                *decode += '1';
                *size += 2;
            }
            else if (param[i * 2 + 0] == '0' && param[i * 2 + 1] == '1') {
                *decode += '0';
                *size += 2;
            }
            else {
                result = false;
                break;
            }
        }
    }
    else {
        if (param[0] == '1') {
            *decode = '0';
            ++*size;
        }
        else if (param[0] == '0') {
            *decode = '1';
            ++*size;
        }
        else {
            result = false;
        }
        if (result) {
            for (i = 0; i < (param.size() - 1) / 2; ++i) {
                if (param[i * 2 + 1] == '1' && param[i * 2 + 2] == '0') {
                    *decode += '1';
                    *size += 2;
                }
                else if (param[i * 2 + 1] == '0' && param[i * 2 + 2] == '1') {
                    *decode += '0';
                    *size += 2;
                }
                else {
                    result = false;
                    break;
                }
            }
        }
    }
    return result;
}

bool debaudot(string const& param, string* decode, int* size)
{
    unsigned char data;
    bool ltrs;
    int raw;
    int bits15;
    string value;
    char temp[16];
    int i;
    int j;
    bool result(true);
    
    decode->clear();
    *size = 0;
    ltrs = true;
    raw = 0;
    bits15 = 0;
    for (i = 0; i < param.size() / 5; ++i) {
        data = 0;
        for (j = 4; j >= 0; --j) {
            data <<= 1;
            if (param[i * 5 + j] == '0') {
                ++*size;
            }
            else if (param[i * 5 + j] == '1') {
                data |= 1;
                ++*size;
            }
            else {
                result = false;
                break;
            }
        }
        if (result) {
            if (raw > 0) {
                bits15 <<= 5;
                bits15 |= data;
                if (--raw <= 0) {
                    snprintf(temp, sizeof(temp), "[%d]", bits15);
                    *decode += temp;
                }
            }
            else {
                value = (ltrs) ? (baudot_table_ltrs[data]) : (baudot_table_figs[data]);
                if (value == "L") {
                    ltrs = true;
                }
                else if (value == "F") {
                    ltrs = false;
                }
                else if (value == "N") {
                    raw = 3;
                    bits15 = 0;
                }
                *decode += value;
            }
        }
        else {
            break;
        }
    }
    return result;
}
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

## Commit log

2014-12-09 initially added
    [mainsoft.xlsx]
2014-12-16 arranged files
    [MORIKAWA_DS.brd, MORIKAWA_DS.sch, OBC_revA.brd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]
2014-12-16 newly added
    [Despatch_BeaconFormat_ver1.0.xls, Despatch_HKFormat_ver1.4.xls, Despatch_LinkMargin_ver1.0.xls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]
2014-12-16 added body CAD data
    [Base_Plate.SLDPRT, Base_Plate2.SLDDRW, Base_Plate2.SLDPRT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]
2014-12-17 fix to avoid using windows prohibited path char
    [main.cpp]
2014-12-17 merged Despatch3DViewer
    [despatch_base.stl, despatch_cover.stl, despatch_pafif.stl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]
2015-01-14 modified with publishing version
    [Aluminium_Cover.SLDPRT, Aluminium_Keel.SLDPRT, Base_Plate.SLDPRT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]
2015-05-04 Updated Despatch3DViewer
    [despatch_base.stl, despatch_cover.stl, despatch_pafif.stl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]
